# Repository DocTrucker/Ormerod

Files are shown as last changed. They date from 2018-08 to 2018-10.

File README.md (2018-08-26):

####

26/08/2018

This repository was been initially cloned from RepRapPro's repository for the 
Ormerod 2 printer. I am predominantly using this as a learning exercise but
hope in the short term to rebuild the PLA kit parts with PETG and resize a few
to reduce the stress fractures that I've experienced with a recent (old) kit 
build. My objectives are different to that of RepRapPro, therefore my ideals 
are different to their ideals. The changes I have made are not to be
interpreted as correcting mistakes, merely working to a different set of goals 
with completely different financial, engineering, and business pressures.

The work here is currently in stage one. I am currently reverse engineering 
the presented STL files into parametric FreeCAD files. My plan is as follows:

1. Re-engineer existing STL files back into a parametric FreeCAD format.
2. Build a basic assembly model to ensure the files are fit fort purpose.
3. Design parts as needed to incorporate an E3D V6 hot end and Bondtech
   Extruder.
4. Build these parts and assemble the first iteration of my take on the
   Ormerod 2.
5. Make the first release of files at this stage.
6. Carry out a written review of the parts and establish objectives to be 
   achieved before the next release.
7. Execute the changes with a modifications categorised into reliability,
   part quality, one off build cost, design for ease of build, and/or build 
   rate.
8. Following release.

I expect that I will move onto a different design of machine after stage 8.

01234567890123456789012345678901234567890123456789012345678901234567890123456789

####

The RepRapPro Ormerod 2 3D Printer design files repository

Licensed under the GPL 3, see: http://www.gnu.org/copyleft/gpl.html

For more information see: https://reprappro.com/shop/reprap-kits/ormerod-2-kit/

Files in this directory were produced in SolidWorks 2015, and is the full assembly for the Ormerod 2. Some components that are shared with our other printers may be found in our "Library" repository.

The 'STLs' directory contains STLs of the printed parts. Instructions for printing parts for Ormerod 2, and a reference - itemising part numbers, descriptions and required quantities - may be found in the Ormerod instructions, here: https://reprappro.com/documentation/ormerod-2/#Printing_parts_for_Ormerod_2

The 'dxf' folder contains the parts in a format for laser cutting.

License GPL

No guarantee is made that the files contained in this project will be free from design faults. The user accepts the risk that some issues may arise from printing and assembling the files contained within this project. Users are however encouraged to publish errors/improvements back to the originator.

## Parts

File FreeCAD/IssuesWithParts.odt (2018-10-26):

Notes on Parts

# 02_548_y-motor-bracket

Overhang to build surface on rear elongated motor bolt hole necessary?

Remove counter sinks

More bracing to hols motor secure.

Use easily accessible idler for tension rather than motor.

Groove bolt hole body could be taller to secure onto the rail better when tightened?

# 15_441_z-gear-driven

Needs to be built with brim.

# 16_492_z-bearing-clamp

(revised) Bolt boss 45 degree slope results in two sharp points trying to meet. Both curl away form intended position.

(revised) Use more of a slope from main body to boss to reduce overhangs.

(revised) Bearing centre to close to base of part.

# 18_440_z-gear

Needs to be built with brim.

# 20_446_extruder-small-gear

Needs to be built with brim.

# 21_xxx_retaining-tongue

No issues. Keying design to prevent incorrect orientation in assembly would help.

# 22_447_extruder-large-gear

Needs to be built with brim.

# 08_549_y-bearing-belt-clamp

Potentially need to lift bearing 0.1mm.

Belt too tight a fit in gripper.

# 09_550_y-bearing-clamp-tagged

Potentially need to lift bearing 0.1mm.

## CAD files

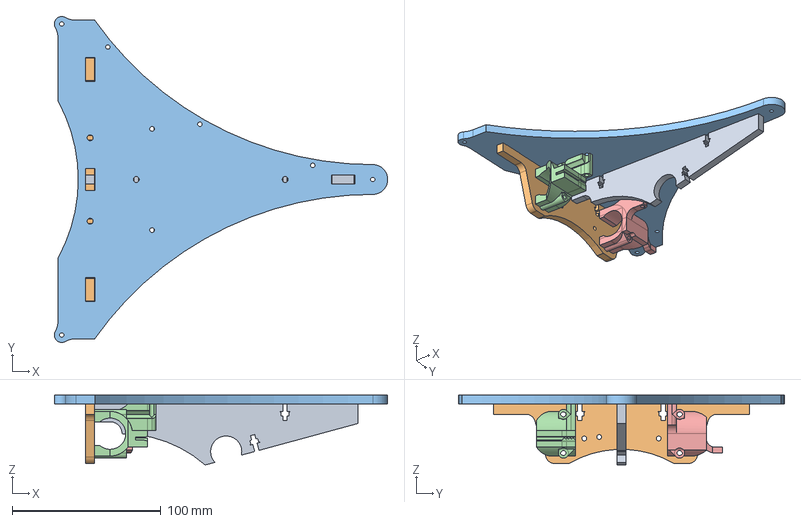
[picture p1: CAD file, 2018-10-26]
FreeCAD/build_surface_assembly.fcstd
224.0 x 219.0 x 47.0 mm

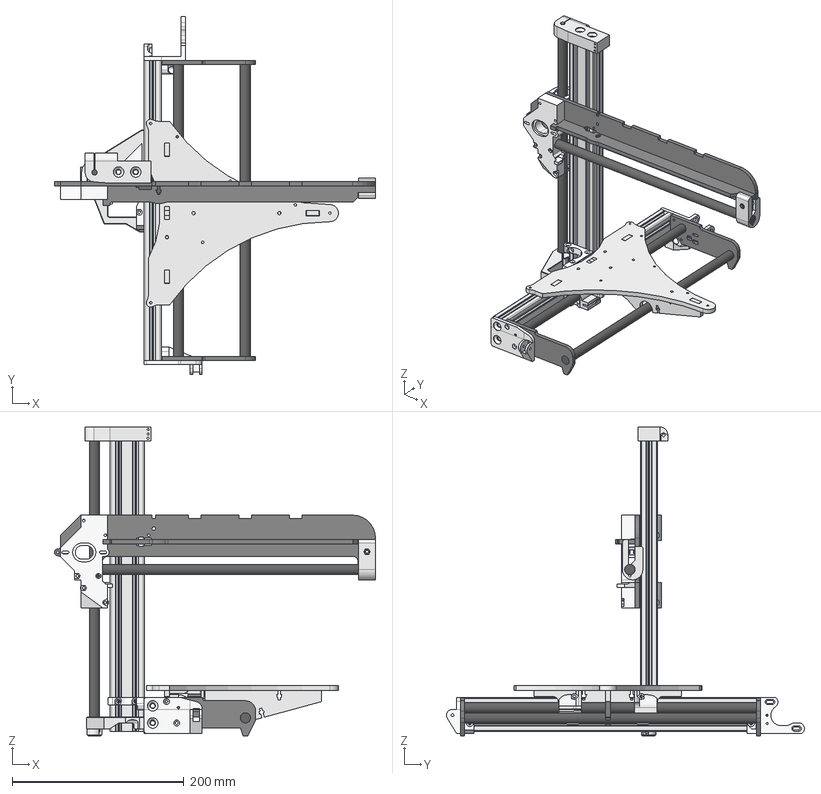
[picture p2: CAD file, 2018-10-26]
FreeCAD/all-in-assembly.fcstd
374.3 x 417.3 x 360.1 mm
y-axis-idler
SmoothRod
SmoothRod001
y-motor-bracket
z-motor-brace
SmoothRod002
SubtractiveLoft002
x-axis-plate
z-bearing-clamp
z-bearing-clamp001
x-rib
x-axis-rod
y-axis-end-plate001
y-axis-end-plate002
x-motor-bracket
z-upper-mount
z-axis-extrusion
y-axis-extrusion
z-lower-mount
x-axis-idler

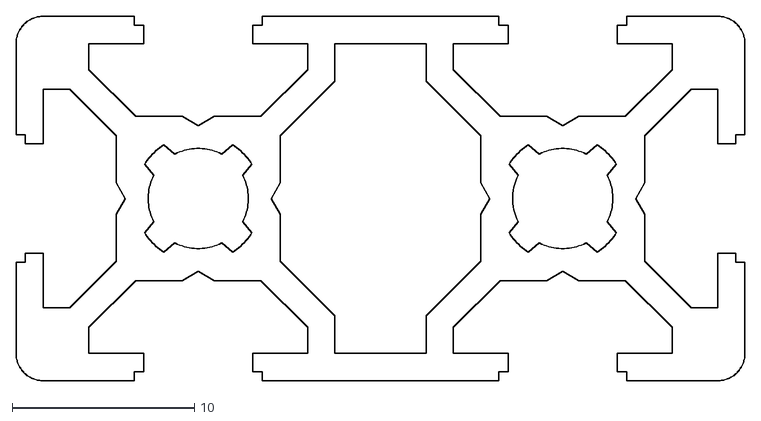
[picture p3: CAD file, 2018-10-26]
dxf/Extrusion_Profile.dxf
40.0 x 20.0

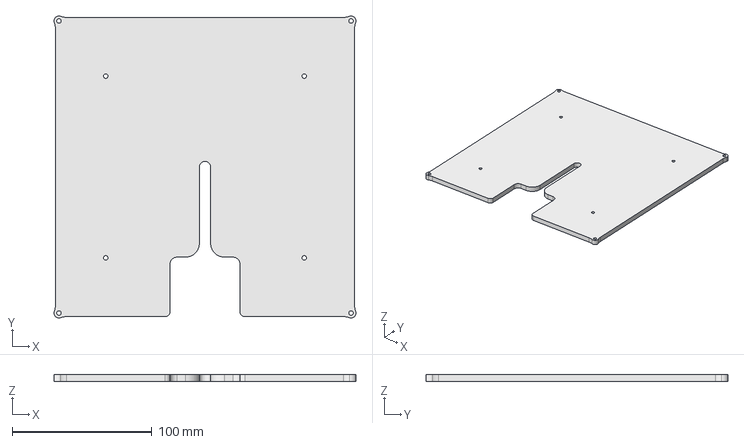
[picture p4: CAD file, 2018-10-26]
FreeCAD/xx_1044_build-surface-base.fcstd
216.1 x 216.1 x 5.00 mm

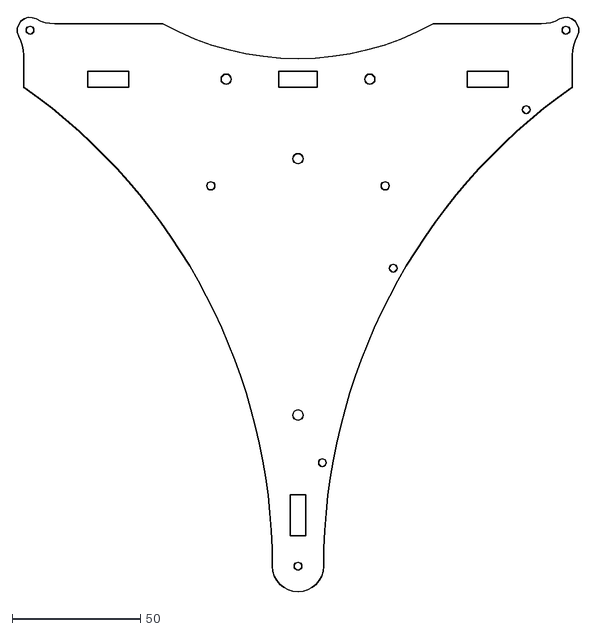
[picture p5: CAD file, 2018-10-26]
dxf/bed.DXF
219.9 x 224.5

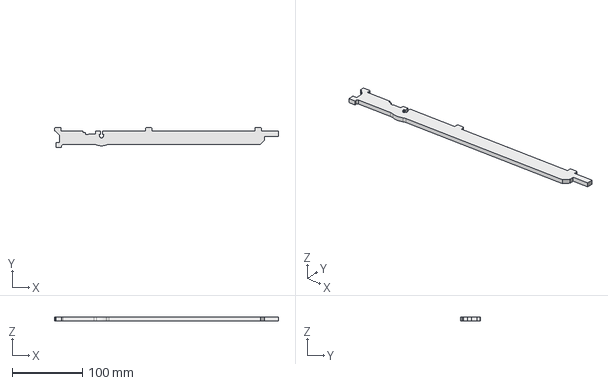
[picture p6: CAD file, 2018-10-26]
FreeCAD/xx_562_x-rib.fcstd
319.5 x 28.0 x 5.00 mm

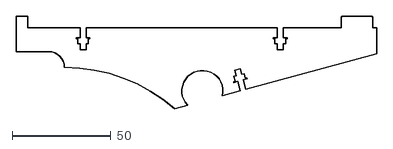
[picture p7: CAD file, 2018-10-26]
dxf/y-cross-rib.DXF
183.0 x 47.0

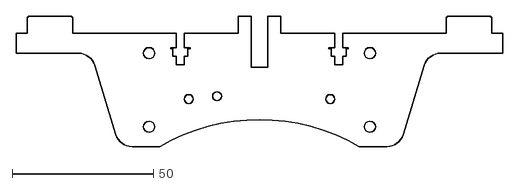
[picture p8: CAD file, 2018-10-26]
dxf/y-rib.DXF
172.0 x 46.0

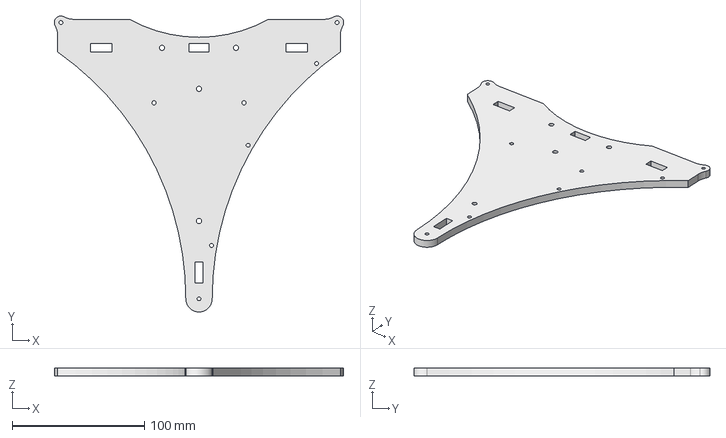
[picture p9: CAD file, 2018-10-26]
FreeCAD/xx_xxx_bed.fcstd
219.0 x 224.0 x 6.00 mm

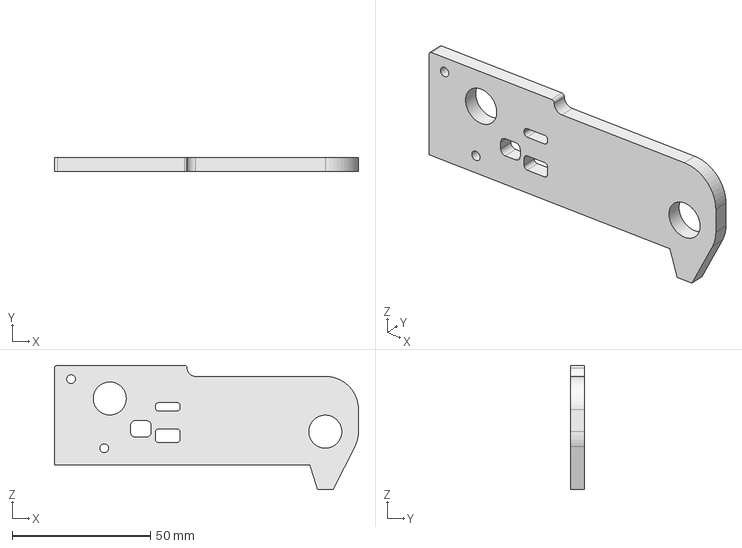
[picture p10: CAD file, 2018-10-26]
FreeCAD/xx_531_y-axis-end-plate.fcstd
110.0 x 5.00 x 45.0 mm

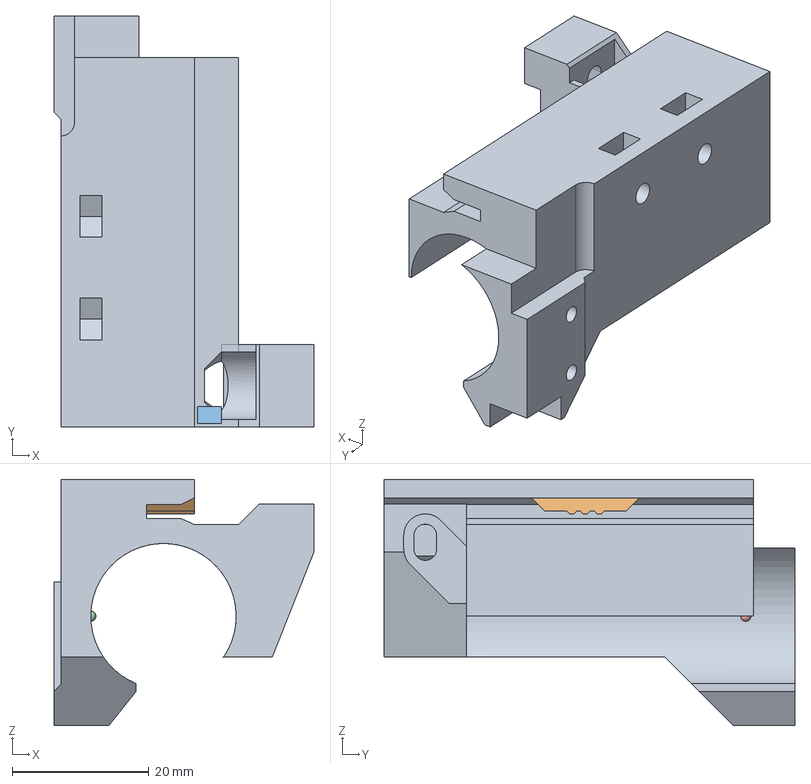
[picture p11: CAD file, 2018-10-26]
FreeCAD/11_546_x-carriage.FCStd
38.0 x 60.0 x 36.0 mm
Main Body
Belt Gripper
XRib Bearing Nut Stop
Lock Sphere 1
Lock Sphere 2

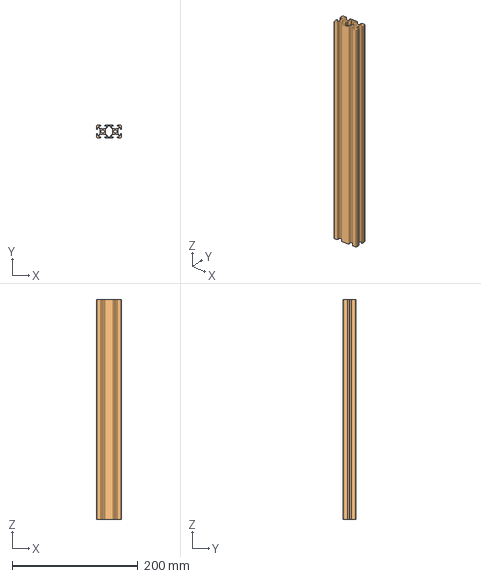
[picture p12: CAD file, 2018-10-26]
FreeCAD/xx_458_aluminimum-extrusion.fcstd
40.0 x 20.0 x 350.0 mm

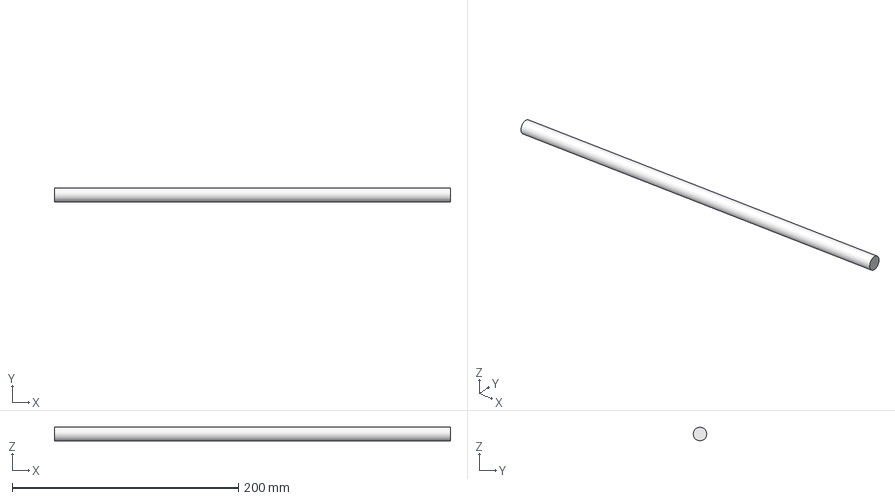
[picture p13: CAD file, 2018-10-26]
FreeCAD/xx_402_smooth-rod.fcstd
350.0 x 12.0 x 12.0 mm

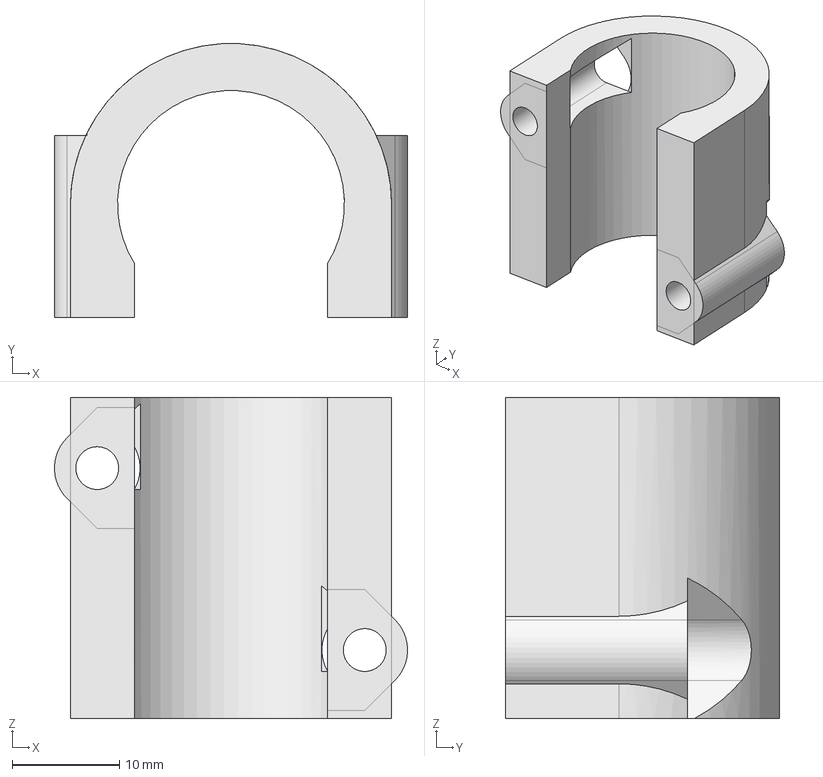
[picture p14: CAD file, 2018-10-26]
FreeCAD/16_492_z-bearing-clamp.FCStd
33.0 x 25.6 x 30.0 mm

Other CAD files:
FreeCAD/14_407_z-runner-mount.FCStd
FreeCAD/10_462_x-idler-bracket.FCStd
FreeCAD/xx_561_x-axis-plate.fcstd
FreeCAD/xx_xxx_y-cross-rib.fcstd
FreeCAD/01_547_y-idler-bracket.FCStd
FreeCAD/02_548_y-motor-bracket.FCStd
FreeCAD/03_469_z-motor-brace.FCStd
FreeCAD/04_437_z-lower-mount.FCStd
FreeCAD/05_438_z-upper-mount.FCStd
FreeCAD/06_527_z-corner-bracket.FCStd
FreeCAD/07_503_z-foot.FCStd
FreeCAD/08_549_y-bearing-belt-clamp.FCStd
FreeCAD/09_550_y-bearing-clamp-tagged.FCStd
FreeCAD/12_473_x-motor-bracket.FCStd
FreeCAD/extruder-drive-cover.fcstd
FreeCAD/xx_xxx_y-rib.fcstd

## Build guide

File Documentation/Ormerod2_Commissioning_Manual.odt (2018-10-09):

Ormerod 2 Build Manual

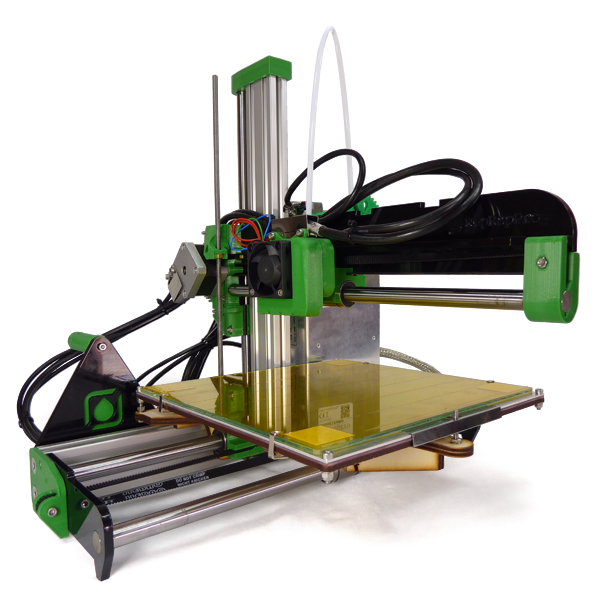
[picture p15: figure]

# Forward

## Credits & License

Original Machine Design: | Jean-Marc Giacalone Adrian Bowyer
Original Documentation: | Ian Stratford
Documentation Conversion to ODT/PDF: | Wesley Brooks
License: | GPL

## Original Documentation Hosts:

Web Archive | https://web.archive.org/web/20160106171632/https://reprappro.com/documentation/ormerod-2/
cheeseandham (RepRap Forum) | http://reprappro.cheeseandham.me.uk/reprappro.com/documentation/index.html

## This Documentation Iteration Host:

DocTrucker GitHub | https://github.com/DocTrucker/Ormerod/tree/master/Documentation

# Ormerod 2

## Overview

The RepRap Pro Ormerod 2 is the latest RepRap self-replicating 3D printer from RepRap Pro. The machine is a faster to assemble, networked 3D printer with non-contact bed probe for full geometric compensation.

These pages are the complete instructions for commissioning and using the RepRapPro Ltd (https://web.archive.org/web/20170716103559/https://reprappro.com/) version of RepRap Ormerod 2. Like all RepRap machines, RepRapPro Ormerod 2 is fully open-source. It is licensed under the GPL. All the design files and software are available from the RepRapPro Ltd Github (https://web.archive.org/web/20170716103559/https://github.com/reprappro/Ormerod) repository.

The RepRapPro Ormerod 2 is fitted with the open-source Duet electronics (https://web.archive.org/web/20170716103559/https://github.com/T3P3/Duet).

## General Notes

## Ormerod 2 Versions

Some sections of the instructions are arranged in tabs, with alternate parts and instructions, depending on the version of your kit. Below is the changelog, which shows the differences between kit versions. The tabs refer to the version number of the Ormerod kit. Your Ormerod kit version number is marked on the sticker on the power supply (on 528.2 and later kits ), or on the x-rib (for earlier kits). Use the LATEST version number – some kits have the 528.2 PSU, but the 528.1 x-rib. Use the set of instructions that relate to your printer.

528.0 | Sept 2014: Original shipping version of Ormerod 2.
528.1 | Oct 2014: Changes to packing. Acrylic fan spacer replaces printed fan-duct and nozzle-duct.
528.2 | Dec 2014: Change to supplied power supply, and added lasercut acrylic parts to mount Duet on new PSU.
528.3 | Feb 2015: Changes to packing.
528.4 | New heated bed design, new bed wiring loom.
528.5 | Ships with new Quick-set nozzle. Separate hot end and fan looms. Cooling fan and duct supplied. Small updates to some printed parts (x-carriage, z-upper-mount, y-motor-mount). Changes to packing.

## Get Support

## Tool List

### Required

Allen keys: 1.5mm, 2mm, 2.5mm, 4mm (the long reach type, with a ‘ball’ hex on the end, are very useful)

### Nice to Have, But Not Necessary

# Commissioning

https://web.archive.org/web/20160106172926/https://reprappro.com/documentation/commissioning-introduction/commissioning-duet/

# Calibration

https://web.archive.org/web/20160106173018/https://reprappro.com/documentation/commissioning-introduction/calibration-duet/

# Printing

https://web.archive.org/web/20160106191341/https://reprappro.com/documentation/commissioning-introduction/printing-duet/

# Maintenance

https://web.archive.org/web/20160106191347/https://reprappro.com/documentation/commissioning-introduction/maintenance-duet/

# Troubleshooting

https://web.archive.org/web/20160106191355/https://reprappro.com/documentation/troubleshooting-introduction/

# Wiring

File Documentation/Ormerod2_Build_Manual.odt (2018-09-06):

Ormerod 2 Build Manual

# Forward

## Credits & License

Original Machine Design: | Jean-Marc Giacalone Adrian Bowyer
Original Documentation: | Ian Stratford
Documentation Conversion to ODT/PDF: | Wesley Brooks
License: | GPL

## Original Documentation Hosts:

Web Archive | https://web.archive.org/web/20160106171632/https://reprappro.com/documentation/ormerod-2/hot-end-assembly-quick-set/
cheeseandham (RepRap Forum) | http://reprappro.cheeseandham.me.uk/reprappro.com/documentation/index.html

## This Documentation Iteration Host:

DocTrucker GitHub | https://github.com/DocTrucker/Ormerod/tree/master/Documentation

# Ormerod 2

## Overview

The RepRap Pro Ormerod 2 is the latest RepRap self-replicating 3D printer from RepRap Pro. The machine is a faster to assemble, networked 3D printer with non-contact bed probe for full geometric compensation.

These pages are the complete instructions for building, commissioning and using the RepRapPro Ltd (https://web.archive.org/web/20170716103559/https://reprappro.com/) version of RepRap Ormerod 2. Like all RepRap machines, RepRapPro Ormerod 2 is fully open-source. It is licensed under the GPL. All the design files and software are available from the RepRapPro Ltd Github (https://web.archive.org/web/20170716103559/https://github.com/reprappro/Ormerod) repository.

The RepRapPro Ormerod 2 is fitted with the open-source Duet electronics (https://web.archive.org/web/20170716103559/https://github.com/T3P3/Duet).

If you want to print the plastic parts for a RepRapPro Ormerod 2, see this web page (https://web.archive.org/web/20170716103559/https://reprappro.com/documentation/ormerod-2/printing/).

## General Notes

BEFORE YOU ATTEMPT TO ASSEMBLE ANY PART OF THE RepRapPro ORMEROD 2 3D PRINTER, PLEASE READ THESE BUILD INSTRUCTIONS FULLY AND ENSURE YOU UNDERSTAND THEM. Although all parts are covered by warranty, this will be invalidated by your not following these build instructions. You are building a complicated machine; many different skills are required to build, to commission and to operate a 3D printer. Try not to rush your build, or you may miss out something vital!

- Give yourself plenty of space and ensure your work area is clean. Dust and dirt are a 3D printer’s worst enemy.
- All printed parts have been printed on RepRapPro’s own machines. Despite the fact that these machines are highly tuned RepRap 3D printers, some holes and features may need a little fettling to get the best performance from the RepRapPro Ormerod 2. There is a video how-to on fettling 3D printed parts here on Vimeo (https://web.archive.org/web/20170716103559/http://vimeo.com/14492980).
- Before you start the build, please ensure you have all the components as listed on the packing list included in the kit. If anything is missing or damaged, please contact us through our contact page (https://web.archive.org/web/20170716103559/https://reprappro.com/support-page/).
- We understand that people may want to change aspects of the machine’s design, and in fact we encourage this as it is one of the benefits of open-source development. Before changing anything, please be aware that the RepRapPro Ormerod 2 has been designed to maximise its build volume relative to the the machine’s footprint, and as such many of its components fit closely to others. So consider your changes carefully before you try to implement them. And when you find improvements, please tell us and the world so that we can include them in future kits, and so that existing owners can upgrade their own machines.
- The RepRapPro Ormerod 2 is a robust RepRap machine once assembled; however it does require a certain amount of care during assembly. If in doubt, force is usually not the answer! There are many ways to get support and advice; see below.

## Ormerod 2 Versions

Some sections of the instructions are arranged in tabs, with alternate parts and instructions, depending on the version of your kit. Below is the changelog, which shows the differences between kit versions. The tabs refer to the version number of the Ormerod kit. Your Ormerod kit version number is marked on the sticker on the power supply (on 528.2 and later kits ), or on the x-rib (for earlier kits). Use the LATEST version number – some kits have the 528.2 PSU, but the 528.1 x-rib. Use the set of instructions that relate to your printer.

528.0 | Sept 2014: Original shipping version of Ormerod 2.
528.1 | Oct 2014: Changes to packing. Acrylic fan spacer replaces printed fan-duct and nozzle-duct.
528.2 | Dec 2014: Change to supplied power supply, and added lasercut acrylic parts to mount Duet on new PSU.
528.3 | Feb 2015: Changes to packing.
528.4 | New heated bed design, new bed wiring loom.
528.5 | Ships with new Quick-set nozzle. Separate hot end and fan looms. Cooling fan and duct supplied. Small updates to some printed parts (x-carriage, z-upper-mount, y-motor-mount). Changes to packing.

## Printing Parts for Ormerod 2

If you have bought the hardware-only version of the Ormerod 2 kit, you will want to print the parts. You may also want to print spare parts for your printer. The list below shows the part number, part name, quantity and location of the parts. Parts are available as STL and SolidWorks files, and there should also be a STEP assembly of the whole printer.

For Ormerod 2, part number 528.0 to 528.4, the easiest place to get the parts is here: https://github.com/reprappro/Ormerod/releases (https://web.archive.org/web/20170716103559/https://github.com/reprappro/Ormerod/releases)

For 528.5 onwards, we use the part number, rather than the name of the part, for the file name. For the latest version of the parts, which should be backwards compatible with all the previous versions, see the Ormerod github repository (https://web.archive.org/web/20170716103559/https://github.com/reprappro/Ormerod). Some parts common to all our machines are in the Library github repository (https://web.archive.org/web/20170716103559/https://github.com/reprappro/Library).

You can download the whole github repository, or download the parts individually; the ‘Location’ in the link below links to the stl page. This will also help you identify the parts. If you download the parts individually, make sure you download the ‘RAW’ version of the file; if you right-click on a link and download, you will end up with a file with the right name (with .stl on the end), but it will actually be an html document!

# | Description | Qty | Location

547 | y-idler-bracket | 1 | Ormerod/STLs (https://web.archive.org/web/20170716103559/https://github.com/reprappro/Ormerod/blob/master/STLs/547.STL)
548 | y-motor-bracket | 1 | Ormerod/STLs (https://web.archive.org/web/20170716103559/https://github.com/reprappro/Ormerod/blob/master/STLs/548.STL)
469 | z-motor-brace | 1 | Ormerod/STLs (https://web.archive.org/web/20170716103559/https://github.com/reprappro/Ormerod/blob/master/STLs/469.STL)
437 | z-lower-mount | 1 | Ormerod/STLs (https://web.archive.org/web/20170716103559/https://github.com/reprappro/Ormerod/blob/master/STLs/437.STL)
438 | z-upper-mount | 1 | Ormerod/STLs (https://web.archive.org/web/20170716103559/https://github.com/reprappro/Ormerod/blob/master/STLs/438.STL)
527 | z-corner-bracket | 1 | Ormerod/STLs (https://web.archive.org/web/20170716103559/https://github.com/reprappro/Ormerod/blob/master/STLs/527.STL)
503 | z-foot | 1 | Ormerod/STLs (https://web.archive.org/web/20170716103559/https://github.com/reprappro/Ormerod/blob/master/STLs/503.STL)
549 | y-bearing-belt-clamp | 1 | Ormerod/STLs (https://web.archive.org/web/20170716103559/https://github.com/reprappro/Ormerod/blob/master/STLs/549.STL)
550 | y-bearing-clamp-tagged | 1 | Ormerod/STLs (https://web.archive.org/web/20170716103559/https://github.com/reprappro/Ormerod/blob/master/STLs/550.STL)
462 | x-idler-bracket | 1 | Ormerod/STLs (https://web.archive.org/web/20170716103559/https://github.com/reprappro/Ormerod/blob/master/STLs/462.STL)
546 | x-carriage | 1 | Ormerod/STLs (https://web.archive.org/web/20170716103559/https://github.com/reprappro/Ormerod/blob/master/STLs/546.STL)
501 | nozzle-mount (one-piece nozzle, 528.4 and before) | 1 | Ormerod/STLs (https://web.archive.org/web/20170716103559/https://github.com/reprappro/Ormerod/blob/528.4/stl/individual%20parts/nozzle-mount.stl)
1079 | nozzle-mount (Quick-set nozzle, 528.5 onwards) | 1 | Ormerod/STLs (https://web.archive.org/web/20170716103559/https://github.com/reprappro/Ormerod/blob/master/STLs/1079.STL)
473 | x-motor-bracket | 1 | Ormerod/STLs (https://web.archive.org/web/20170716103559/https://github.com/reprappro/Ormerod/blob/master/STLs/473.STL)
407 | z-runner-mount | 1 | Ormerod/STLs (https://web.archive.org/web/20170716103559/https://github.com/reprappro/Ormerod/blob/master/STLs/407.STL)
441 | z-gear-driven | 1 | Ormerod/STLs (https://web.archive.org/web/20170716103559/https://github.com/reprappro/Ormerod/blob/master/STLs/441.STL)
440 | z-gear | 1 | Ormerod/STLs (https://web.archive.org/web/20170716103559/https://github.com/reprappro/Ormerod/blob/master/STLs/440.STL)
492 | z-bearing-clamp | 2 | Ormerod/STLs (https://web.archive.org/web/20170716103559/https://github.com/reprappro/Ormerod/blob/master/STLs/492.STL)
425 | z-nut-trap | 1 | Ormerod/STLs (https://web.archive.org/web/20170716103559/https://github.com/reprappro/Ormerod/blob/master/STLs/425.STL)
554 | Extruder drive block | 1 | Ormerod/STLs (https://web.archive.org/web/20170716103559/https://github.com/reprappro/Ormerod/blob/master/STLs/554.STL)
446 | Extruder small gear | 1 | Ormerod/STLs (https://web.archive.org/web/20170716103559/https://github.com/reprappro/Ormerod/blob/master/STLs/446.STL)
447 | Extruder large gear | 1 | Ormerod/STLs (https://web.archive.org/web/20170716103559/https://github.com/reprappro/Ormerod/blob/master/STLs/447.STL)
152 | Tongue | 1 | Library/STLs (https://web.archive.org/web/20170716103559/https://github.com/reprappro/Library/blob/master/STL/152.STL)
820 | PSU cover | 1 | Library/STLs (https://web.archive.org/web/20170716103559/https://github.com/reprappro/Library/blob/master/STL/820.STL)
821 | PSU brace | 1 | Ormerod/STLs (https://web.archive.org/web/20170716103559/https://github.com/reprappro/Ormerod/blob/master/STLs/821.STL)
442 | Spool spigot | 1 | Ormerod/STLs (https://web.archive.org/web/20170716103559/https://github.com/reprappro/Ormerod/blob/master/STLs/442.STL)
525 | Spool clip | 1 | Ormerod/STLs (https://web.archive.org/web/20170716103559/https://github.com/reprappro/Ormerod/blob/master/STLs/525.STL)
1123 | Cooling fan duct | 1 | Ormerod/STLs (https://web.archive.org/web/20170716103559/https://github.com/reprappro/Ormerod/blob/master/STLs/1123.STL)

## Get Support

If you find you need help or advice with assembling, commissioning or using your RepRapPro Ormerod 2 3d printer, you can use the following channels:

- Check the instructions again; we are regularly updating them with feedback from our growing user-base.
- Contact the support department of the company that sold you your printer.
- Check the RepRap community forum, Ormerod section (https://web.archive.org/web/20170716103559/http://forums.reprap.org/list.php?340).
- Contact us on our irc (internet relay chat) channel RepRapPro (https://web.archive.org/web/20170716103559/http://webchat.freenode.net/?channels=reprappro) on freenode irc
- Contact us via email; see our contact page (https://web.archive.org/web/20170716103559/https://reprappro.com/support-page/).

## Archived Documents for Older Versions

If you have an older RepRapPro Ormerod and want a past copy of this documentation see these links:

- RepRapPro Ormerod 1 Instructions (https://web.archive.org/web/20170716103559/https://reprappro.com/documentation/ormerod/)

## Tool List

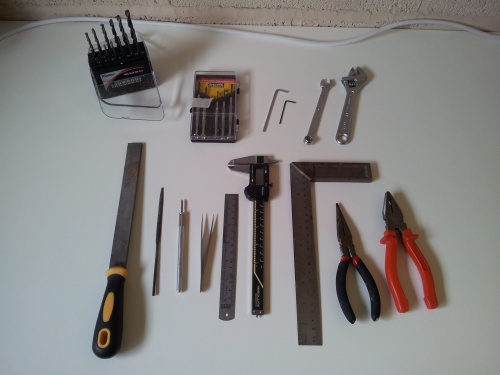
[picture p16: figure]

Tools required for the build of the RepRapPro Ormerod 2 3D printer:

### Required

Allen keys: 1.5mm, 2mm, 2.5mm, 4mm (the long reach type, with a ‘ball’ hex on the end, are very useful)

- Medium, cross-head screwdriver
- 8mm (M5) socket and/or spanner
- 15cm adjustable spanner
- Fine tweezers
- Ruler, at least 300mm
- Fine-nosed pliers
- Scissors
- Drill: 2mm
- Hand chuck, pin vice or small electric drill
- Small, flat-bladed, electrical screwdriver
- Pencil sharpener
- Digital Multimeter
- Hot air gun, or cigarette lighter (or other heat source such as a gas cooker ring for heating PTFE heatshrink; a hair dryer is not sufficient)

### For Adjusting Plastic Parts, if Necessary

- Drills: 3mm, 4mm
- File
- Half round needle file
- Sharp craft knife

### Nice to Have, But Not Necessary

# 5.5mm (M3) socket and/or spanner

- Vernier or digital callipers

# Y Axis Assembly

## Y axis sub-assemblies

### Y-idler-end

TIP: There’s a list of the Ormerod printed parts on THIS PAGE (https://web.archive.org/web/20161108033219/https://reprappro.com/documentation/ormerod-2/). Click on the ‘Location’, to see a preview of the printed part, if you’re not sure what it is.

# | Component | Qty | Type

| y-idler-bracket | 1 | Printed
| y-axis-end-plate ‘A’ | 1 | Lasercut
| M4x12mm countersunk socket head screw | 1 | Fastener
| M4 T-nut | 1 | Fastener
| M3x12mm countersunk socket head screw | 2 | Fastener
| M3 Nut | 2 | Fastener
| M3x12mm cap head screw | 1 | Fastener
| 623 bearing (10mm diameter) | 1 | Fastener

TIP: Click on pictures in the instructions to see a larger version. Right-click and select ‘Open link in new Tab’ to see the full size image.

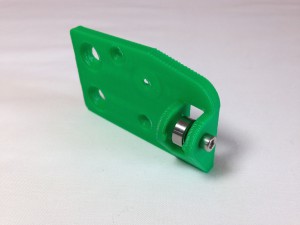
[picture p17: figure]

Fit the 623 idler bearing to the y-idler-end. It may require a fair bit of force to push the bearing into position. It is held in place by a M3x12mm cap head screw. This should self-tap into the printed part, with no need for a nut on the free end.

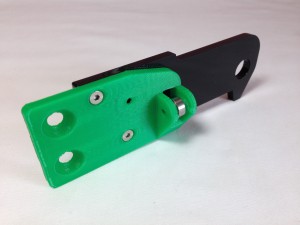
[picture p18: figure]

Using the M3x12mm countersunk socket head screws, assemble the y-axis-end-plate ‘A’ with the y-motor-bracket, with an M3 nut on the back of each screw.

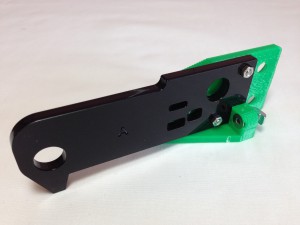
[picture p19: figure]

The M4x12mm countersunk socket-head screw goes through the y-idler-mount as shown, with the T-nut on the other side. Leave the T-nut loose – it connects with the aluminium extrusion.

### Y-motor-end

# | Component | Qty | Type

| y-motor-bracket | 1 | Printed
| y-axis-end-plate ‘B’ | 1 | Lasercut
| M4x12mm countersunk socket head screw | 1 | Fastener
| M4 T-nut | 1 | Fastener
| M3x12mm countersunk socket head screw | 2 | Fastener
| M3 Nut | 2 | Fastener

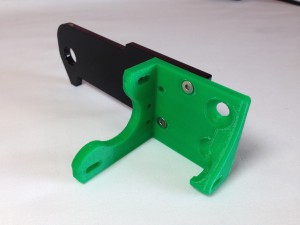
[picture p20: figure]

Begin by assembling the Y-motor-end. Use y-axis-end-plate ‘B’ (there is a small ‘B’ engraved on one side of the plate) with the y-motor-bracket. As the y-axis-end-plate is laser-cut acrylic, the 12mm holes will be slightly larger in diameter on one side of the y-axis-end-plate (the side with the letter ‘B’) which will make it easier to insert the 12mm ground steel bar later.

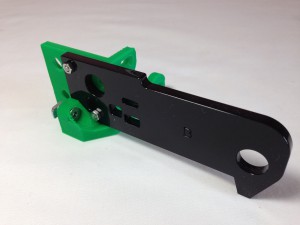
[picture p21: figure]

Using the M3x12mm countersunk socket-head screws, connect the two parts together as shown, with an M3 nut on the back of each..

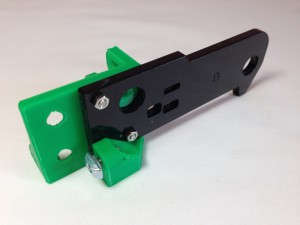
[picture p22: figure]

The M4x12mm countersunk socket-head screw goes through the y-motor-mount as shown, with the T-nut on the other side. Leave the T-nut loose – it connects with the aluminium extrusion.

## Y axis frame

The next step is to assemble the Y axis frame. For this you will need the following:

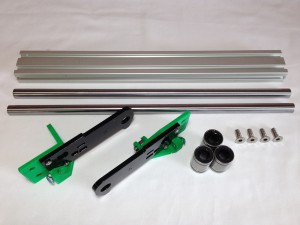
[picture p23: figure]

# | Component | Qty | Type

| y-motor-end | 1 | Assembled
| y-idler-end | 1 | Assembled
| Aluminium extrusion | 1 | Hardware
| Smooth rod 12x350mm | 2 | Hardware
| LM12UU Linear bearing | 3 | Hardware
| M6x16mm countersunk socket head screw | 4 | Fastener

Screw the y-idler-end onto the aluminium extrusion, using two M6x16mm countersunk socket screws. These screws need to be tight – if they are loose, the Y-ends will move in relation to the aluminium extrusion, and the X axis will not be level to the bed.
On the inside of the y-idler-end, check that the M4 T-nut is located in the extrusion slot.
As you tighten the screw, the T-nut should rotate 90 degrees in the extrusion, from horizontal to vertical. It may need a little help! If it can’t rotate, it may have started too close to the printed part; loosen the screw off a couple of turns, then try tightening again. Once it has rotated so that it is vertical, fully tighten the screw.
With the y-idler-end supported by the edge of a table, take one of the 12x350mm smooth rods and push it into the hole in the acrylic end piece that is closest to the aluminium extrusion. The 12mm diameter holes are sized to be an interference fit with the rods, and the Acrylic laser cut plates are quite brittle so care must be taken when inserting the rods not to break the end plates. You can use a piece of wood, or soft-faced hammer, to tap gently on the end of the rod, if necessary.
NOTE: Some 12x350mm smooth rods may be a little longer, due to variability in manufacture. The y-idler-end printed part can accommodate this, with a pocket. The other places that the rods are used can similarly accommodate these rods (Z axis), or it doesn’t matter (X axis, Y axis front rod) – the longer rod will simply poke out the end a millimetre or so.
With the acrylic supported, push the second 12x350mm smooth rod into the hole in the end of the plate. Keep the rod perpendicular to the plate whilst pushing. Try to keep both rods upright, so they do not stress the holes in the Acrylic.
Slide the LM12UU Linear bearings onto the smooth rod. Put two onto the rod closest to the aluminium extrusion, and one on the front rod. Check they slide smoothly and freely.
Push the y-motor-end onto the smooth rods at the other end. This may be easiest with the Y axis vertical. Make sure the acrylic part is supported when pushing the rods in. Try and keep the smooth rods as straight as possible, to avoid damaging the acrylic parts. Push them home, so that the motor mount is flush with the aluminium extrusion. Again, only tap them in with a piece of wood, or soft-face hammer, to avoid damaging the parts.
Screw the y-motor-end onto the aluminium extrusion, using two M6x16mm countersunk socket screws. These screws need to be tight – if they are loose, the X axis will not be level to the bed.
Ensure the M4 T-nut is located in the extrusion slot, and tighten.
The completed assembly. Check all screws are tight.

## Y Axis Motor

Now you can fit the Y axis motor. For this step you will need the following:

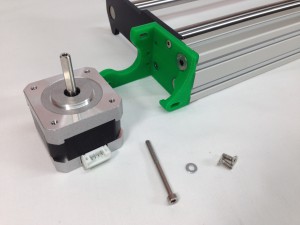
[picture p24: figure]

# | Component | Qty | Type

| y-axis-frame | 1 | Assembled
| NEMA17 stepper motor | 1 | Hardware
| M3x8mm countersunk socket screw | 2 | Fasteners
| M3x40mm cap head screw | 1 | Fasteners
| M3 washer | 1 | Fasteners

One screw needs to be removed from the back of the motor, as shown. Don’t lose this M3x26mm crosshead screw; we’ll be using it for the y-carriage.
Fit the motor into the printed y-motor-bracket. Secure the motor in place with 2 x M3x8mm countersunk socket screws in the front face.
Put one M3x40mm cap head screw with an M3 washer, in the back of the motor, where you took out the motor screw.
The three screws of the motor are mounted in slots, so you can slide the motor a small distance. This allows you to adjust the belt tension, once the belt is fitted. Leave the screws hand tight with the motor at the right-hand end of the slots in the picture.
The completed y axis assembly.

# Z Axis Assembly

As with the Y axis, the Z axis is assembled in stages, starting with small sub-assemblies which are brought together towards the end.

## Z Axis Sub-Assemblies

### Z-motor-mount

Begin with the z-motor-mount. You will need the following parts:

# | Component | Qty | Type

| z-motor-brace | 1 | Printed
| NEMA17 stepper motor | 1 | Hardware
| M3x8mm countersunk socket screw | 1 | Fastener
| M3 washer | 1 | Fastener
| 623 bearing (10mm diameter) | 1 | Hardware
| M3x12mm countersunk socket screw | 3 | Fastener
| M4x12mm countersunk socket screw | 3 | Fastener
| M4 T-nut | 3 | Fastener

Begin by securing the 623 bearing on the corner of the Z motor, with an M3x8mm countersunk socket screw. The connector at the bottom of the motor shows which corner to use. The M3 washer goes between the bearing and the motor body; check the bearing can rotate freely.
Loosely fit the M4 T-nuts with the M4x12mm countersunk screws to the z-motor-brace. Then screw the stepper motor to the z-motor-brace using the M3x12mm countersunk screws, as shown.

### Z-lower-mount

The z-lower-mount sub-assembly requires the following:

# | Component | Qty | Type

| z-lower-mount | 1 | Printed
| M4x12mm countersunk socket screw | 3 | Fastener
| M4 T-nut | 3 | Fastener

Loosely fit the M4 T-nuts as shown

### Z-upper-mount

The z-upper-mount sub-assembly requires the following:

# | Component | Qty | Type

| z-upper-mount | 1 | Printed
| M3x35mm cap head screw | 1 | Fastener
| M3 nut | 1 | Fastener

Fit the M3 screw and nut as shown.

### Z-corner-bracket (528.5 onwards)

The z-corner-bracket sub-assembly requires the following:

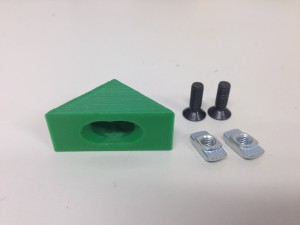
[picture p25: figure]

# | Component | Qty | Type

| z-corner-bracket | 1 | Printed
| M4x10mm countersunk socket screw | 2 | Fastener
| M4 T-nut | 2 | Fastener

Now loosely fit two M4 T-nuts using M4x10mm countersunk socket screws into the z-corner-bracket.

### Z-corner-bracket (528.0 to 528.4)

The z-corner-bracket sub-assembly requires the following:

# | Component | Qty | Type

| z-corner-bracket | 1 | Printed
| M4x12mm countersunk socket screw | 2 | Fastener
| M4 T-nut | 2 | Fastener

Now loosely fit two M4 T-nuts using M4x10mm countersunk socket screws into the z-corner-bracket.

## Z axis assembly

You can now bring all of the Z axis sub-assemblies together, using the following parts:

# | Component | Qty | Type

| z-motor-mount | 1 | Assembled
| z-lower-mount | 1 | Assembled
| z-upper-mount | 1 | Assembled
| z-corner-bracket | 1 | Assembled
| LM12UU linear bearing | 2 | Hardware
| Smooth rod 12x350mm | 1 | Hardware
| Aluminium extrusion | 1 | Hardware
| M6x16mm countersunk socket screw | 2 | Fastener

NOTE: THERE IS NO NEED TO SLIDE THE T-NUT IN FROM THE END OF THE ALUMINIUM EXTRUSION!
The M4 T-nuts are designed to drop into the extrusion slot. As the retaining screw is tightened, the T-nut rotates 90 degrees in the slot and locks into place.

Start by putting the z-upper-mount on the aluminium extrusion – it’s a tight fit. Try to put it on as squarely as possible, to avoid damaging the printed part. If you need to, use a wooden block or soft-faced hammer if you’re going to tap the aluminium extrusion, to avoid damage to the aluminium!
Check the aluminium extrusion is all the way in to the z-upper-mount. Secure the z-upper-mount with two M6x16mm countersunk screws.
Fit the 12x350mm smooth rod into the z-upper-mount. You may need to slacken off the clamp screw to get it in. Make sure it is pushed in as far as it will go; it should be level with the end of the aluminium extrusion. Tighten the clamp screw.
Slide the LM12UU Linear bearings onto the smooth rod. Check they slide smoothly and freely.
Slide the z-motor-mount sub-assembly onto the end of the extrusion. Keep all of the M4 T-nuts loose to allow for moving the motor around.
The z-lower-mount goes around the motor, and it’s easiest to put them on together.
Hook the z-lower-mount over the motor, and move them together up the aluminium extrusion. The smooth rod should engage in the hole of the z-lower-mount; make sure it is pushed on as far as possible.
Lightly tighten the two M4 T-nuts on the z-motor-mount that are engaged in the aluminium profile slot. The M4 T-nuts should not be done too tight at this stage; just enough to hold the Z motor to the extrusion.
The assembly from another angle. Try to orientate the T-nuts horizontally, so they can drop into the Y axis aluminium extrusion easily.
The complete Z axis assembly.

## Connecting the z axis assembly to the y axis assembly

On the Y axis idler side, measure 210mm from the end of the Y axis aluminium extrusion without the Y axis motor, and mark with a pencil. This is to mark where the Z axis will be connected.
On the Y axis motor side, measure 120mm from the end of the Y axis aluminium extrusion, and mark with a pencil. The Z extrusion will sit between these two marks.
The Z axis assembly can now be attached to the Y axis assembly. Orientate the Z nuts so they drop into the extrusion; you don’t need to slide them on from the end.
Tighten the three M4 countersunk screws on the z-lower-mount first. As you tighten them, the T-nuts should rotate 90 degrees and catch in the extrusion slot. They may need a wiggle to get them to turn. Do the middle one shown in the picture first; it’s the most difficult, as you can’t see if it catches, but the axis will hold when it does. Assemble loosely to start with, so you can move the components to the correct places.
The base of the vertical aluminium extrusion must be flush with the bottom of the Y axis extrusion. The bottom of the motor will be a couple of millimetres below the level of the extrusions.
Try to get the extrusion between the two marks on the Y axis aluminium extrusion, so it’s in the right place.
Use the supplied set square to check the Z axis and Y axis extrusions are at right angles to each other. Tighten the z-motor-mount to the two extrusions, then attach and tighten the z-corner-bracket, which gives additional support (shown on the left side of the Z extrusion). Repeat the above alignment steps to confirm they are all correct, before fully tightening all the fasteners.

## Attaching the z-foot

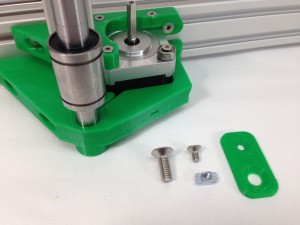
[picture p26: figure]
ORM2-z-axis-build-08

# | Component | Qty | Type | (https://web.archive.org/web/20161108034630/https://reprappro.com/wp-content/uploads/2014/05/ORM2-z-axis-build-08.jpg)

| ZY assembly | 1 | Assembled
| z-foot | 1 | Printed
| M6x16mm countersunk socket screw | 1 | Fastener
| M4x8mm countersunk socket screw | 1 | Fastener
| M4 T-nut | 1 | Fastener

The base of the vertical aluminium extrusion should be flush with the bottom of the Y axis extrusion. These two can then be secured using the z-foot, one M6x16mm countersunk socket screw, and an M4 T-nut and M4x8mm countersunk socket screw.

# Y Carriage

## Y carriage assembly

The Y carriage can now be assembled and fitted. You will need the following parts:

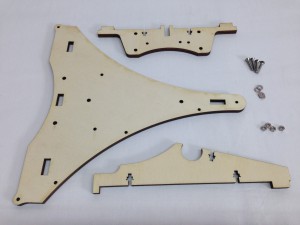
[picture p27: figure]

# | Component | Qty | Type

| bed-support (6mm ply) | 1 | Laser cut
| y-axis-rib (6mm ply) | 1 | Laser cut
| y-axis-cross-rib (6mm ply) | 1 | Laser cut
| M3x16mm countersunk socket screw | 4 | Fastener
| M3 nut | 4 | Fastener
| M3 washer | 4 | Fastener

The y-axis-rib and y-axis-cross rib slot into the bed-support. Make sure the holes in the edge of the bed-support are on the left; these are used to attach the bed wiring later.
Secure the bed-support to the Y axis ribs using the four M3x16mm countersunk socket screws. An M3 washer and M3 nut go in the captive holes of the Y axis ribs. The easiest way to do this is to hold the bed vertically, and put your finger under the hole. Drop the washer in, then the nut.
Then thread the M3x16mm countersunk socket screw through from the top of the bed-support, so it engages with the nut. Repeat for the other three nut traps between the ribs and bed-support. Tighten all of them.
Make sure the bed-insulator is orientated correctly, as shown in the picture. The holes for the wiring are on the right-hand side when the y-carriage is the correct way up as in this picture.

## Y carriage mounting

Fit the y-carriage to the assembled y-z-axis assembly. The following parts are required:

# | Component | Qty | Type

| y-z-axis assembly | 1 | Assembled
| y-carriage assembly | 1 | Assembled
| y-bearing-belt-clamp | 1 | Printed
| y-bearing-clamp-tagged | 1 | Printed
| M3x30mm cap head screw | 4 | Fastener
| M3x25mm countersunk socket screw | 1 | Fastener
| M3x26mm crosshead screw (removed from NEMA17 motor) | 1 | Fastener
| M3 nut | 6 | Fastener

Push the two bearings on the back Y rod to the extreme ends of the carriage. This gives you the space you need to mount the y-carriage.
Take an M3x30mm cap head screw, and thread it through the lower hole of the y-bearing-clamp. Note the orientation of the y-bearing-clamp in the picture. Using a pair of pliers (or fingers if they are small enough!) with an M3 nut, mount the clamp on the y-carriage, around the back smooth rod, as shown.
This can be quite fiddly! But it’s much easier without the bearings in the y-bearing-clamps. Lightly tighten the screw, as it will be easier to push the bearing in.
Lift the y-carriage up to allow you to hold an M3 nut in position, with pliers, to fix another M3x30mm cap head screw through the top hole in the y-bearing-mount.
Repeat the process for the y-bearing-mount on the other side, noting the orientation. Slide the back bearings into the y-bearing-clamps.
Note the position of the mount on the bearing. This is important to allow maximum movement of the Y axis in its frame. Slide the front bearing sideways into the notch in the Y carriage.
Using the M3x26mm crosshead screw your removed from the y-axis NEMA17 motor, push this up through the y-bearing-clamp-. If you put it in from the top, it will get in the way of the belt.
Secure with an M3 nut on top of the bed-support.
On the other side, thread a M3x25mm countersunk screw down through the bed-support, through the y-bearing-clamp, and secure with an M3 nut.
Tighten all six clamp screws. While doing this, slide the y-carriage up and down the smooth rods; this help centre the bearings, and lets the carriage slide smoothly. The picture shows the finished assembly.

## Y axis drive belt

# | Component | Qty | Type

| 1/4″ MXL Belt | 1 | Hardware
| MXL pulley | 1 | Hardware
| M3 grub screw | 1 | Hardware
| Microswitch | 1 | Electronics
| M2.5x10mm cap head screw | 2 | Electronics

The 1/4″ MXL belt is supplied as one piece. Measure it with a tape measure, and cut the MXL belt to at least 710mm for the X axis, making sure you have at least 830mm left for the Y axis. There should be more belt than you need, but DO NOT just cut it in half – it may leave with you with too little for the Y axis!
Mount the microswitch with the two M2.5x10mm cap head screws. These should self-tap into the plastic of the y-motor-mount. Do not widen these holes with a drill, or the screws won’t hold.
The switch should align with the hole in the laser cut y-axis-end-plate. Check the tab on the y-bearing-clamp hits the switch at the end of its travel.
Screw the grub screw partially into the pulley. The motor shaft has a flat on it; align the grub screw with this.
Put the pulley on the motor shaft, and tighten the grub screw using a 1.5mm Allen key.
Thread the belt through the top hole in the y-axis-end-plate, around the drive pulley, and back through the lower slot in the y-axis-end-plate. The teeth of the belt should mesh with the teeth of the pulley.
Thread the belt along the length of the Y axis. Twist the belt 180 degrees before feeding it through the through the lower slot in the idler end y-axis-end-plate, around the bearing, and back through the top slot. The twist in the belt means it will run on the bearing on the back of the belt.
The twist in the belt also means the teeth of the belt can interlock. This is used to join the belt, and fix it to the y-carriage. Pull the belt tight, interlock the teeth, then push the two belt ends into the y-bearing-clamp, as shown.
One end of the belt should finish in the clamp, while any extra belt is free to come out the end of the clamp. Adjust the belt until it is as tight as possible. It will probably still be a little loose; don’t worry, you will be able to adjust the tension.
Cut off the excess belt. Leave about 10mm projecting; you may need to remove and re-fit it one day.

## Y belt tensioning

The belt tension needs to be quite tight, or the axis will suffer from backlash, and you will not get smooth vertical walls in your prints. But the belt should not be too tight, or the motor will struggle to move the axis! To adjust the belt tension, the y-axis motor is mounted in slots. Loosen the three screws, and pull the motor away from the mount to increase the belt tension. Re-tighten the screws, keeping the motor square to the axis. It is sometimes easier to get someone to help you with this, as more than two hands are useful.
When you twang the bottom belt, which has the longest uninterrupted span, a just-audible note should be heard. For reference, the note of the lowest string of a bass guitar is suitable. This is the bottom ‘E’ string (https://web.archive.org/web/20161108040356/http://www.tunemybass.com/); search online for another audio example for reference, if you need it. Adjust the belt as required.
The completed assembly.

# X Axis Assembly

## X axis sub-assemblies

The first step is to assemble a couple of sub assemblies.

### X-axis-motor

The x-axis-motor moves the x-axis belt.

# | Component | Qty | Type

| NEMA17 motor | 1 | Hardware
| MXL pulley | 1 | Hardware
| M3 grub screw | 1 | Hardware

Screw the grub screw partially into the pulley. The motor shaft has a flat on it; align the grub screw with this. For the X axis, the pulley goes on the shaft with the pulley teeth closest to the motor body.
Put the pulley on the motor shaft, and tighten the grub screw using a 1.5mm Allen key. The pulley needs to sit right on the very end of the motor shaft, as shown in the picture.

### X-idler

The x-idler is at the other end of the x-axis from the x-motor, and carries the bearing for the x-axis belt.

# | Component | Qty | Type

| x-idler-bracket | 1 | Printed
| 623 bearing (10mm diameter) | 1 | Hardware
| M3x25mm countersunk socket screw | 1 | Fastener
| M3 Nut | 1 | Fastener

Push the countersunk screw through the x-idler-bracket. The hole may be a little tight where it breaks through to the gap in the middle of the x-idler-bracket. Place the bearing inside the x-idler-bracket and fit the M3 nut to the protruding screw.
Pull the M3 nut into the ‘nut trap’, but leave the assembly loose at this stage. A ‘nut trap’ is a hole in a printed part that is designed to hold a nut ‘captive’.

### X-carriage (528.5 Onwards)

The x-carriage is connected to the x-axis belt, and travels along the X axis, carrying the hot end.

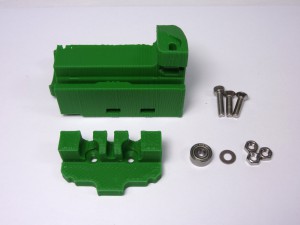
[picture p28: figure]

# | Component | Qty | Type

546.1 | x-carriage | 1 | Printed
1079 | Quick-set nozzle-mount | 1 | Printed
423 | MR93ZZ bearing (9mm diameter) | 1 | Hardware
257 | M3x12mm cap head screw | 1 | Fastener
212 | M3 washer | 1 | Fastener
258 | M3 Nut | 3 | Fastener
466 | M3x12mm countersunk socket screw | 2 | Fastener

Fit the bearing using the M3x12mm cap head screw. IMPORTANT: use a 3mm drill to clean the slot that the screw goes through; this allows you to adjust the angle of the hot end. When it is loosened off the screw needs to be able to slide in the slot.
The M3 washer should be positioned between the bearing and the x-carriage.
The M3 nut is quite fiddly to fit. It should be possible to tighten it without using a tool on it, as the flat of the nut rests against the shoulder in the printed part.
Put an M3 nut in each of the nut traps.
Attach the nozzle mount as shown with two M3x12mm countersunk socket screws.
With this version of the x-carriage, the bearing runs on the underside of the x-axis plate, rather than on the back of it. This reduces the amount of flex of the x-axis-plate.

### X-carriage (528.0 to 528.4)

The x-carriage is connected to the x-axis belt, and travels along the X axis, carrying the hot end.

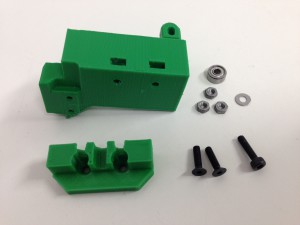
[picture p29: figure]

# | Component | Qty | Type

546 | x-carriage | 1 | Printed
501 | nozzle-mount | 1 | Printed
423 | MR93ZZ bearing (9mm diameter) | 1 | Hardware
257 | M3x12mm cap head screw | 1 | Fastener
212 | M3 washer | 1 | Fastener
258 | M3 Nut | 3 | Fastener
466 | M3x12mm countersunk socket screw | 2 | Fastener

Fit the bearing using the M3x12mm cap head screw. The M3 washer should be positioned between the bearing and the x-carriage. IMPORTANT: use a 3mm drill to clean the slot that the screw goes through; this allows you to adjust the angle of the hot end. When it is loosened off the screw needs to be able to slide in the slot.
Put an M3 nut in each of the nut traps. Attach the nozzle mount as shown with two M3x12mm countersunk socket screws.

## X axis assembly

Now you can start to assemble the X axis.

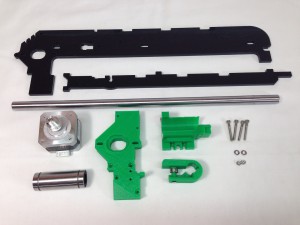
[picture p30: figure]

# | Component | Qty | Type

| x-carriage | 1 | Assembled
| x-idler | 1 | Assembled
| x-axis motor | 1 | Assembled
| x-motor-bracket | 1 | Printed
| x-axis-plate | 1 | Laser cut
| x-rib | 1 | Laser cut
| Smooth rod 12x350mm | 1 | Hardware
| LM12LUU linear bearing | 1 | Hardware
| M3x25mm cap head screw | 4 | Fasteners
| M3 Nut | 2 | Fasteners
| M3 washer | 2 | Fasteners

Push the x-rib into place in the slots in the x-axis-plate, which should slot together easily. DO NOT FORCE! Acrylic is quite brittle, and you may break the x-rib. Use a file to smooth any rough edges, and ease the tabs of the x-rib, so it goes into the x-axis-plate easily. The x-axis-plate should be perfectly flat; if it is bowed or twisted, the x-carriage will not run straight and true.
Make sure the screw through the x-idler sub-assembly is loose. Push the x-idler onto the end of the x-axis-plat and x-rib as shown, making sure it goes on straight.
Slide the smooth rod into the x-motor-bracket.
Then slide the linear bearing onto the bar, then the x-carriage. You need to fit the x-carriage now, as it won’t fit on once the smooth rod is connected to the x-idler (next step). Don’t push the x-carriage onto the bearing yet, as it needs to be off the bearing to attach the x-axis-drive-belt.
Push the smooth rod into the x-idler. Be careful not to bend or twist the acrylic parts.
Push the x-motor-bracket until it buts up to the x-rib. Ensure you have the parts lined up before applying too much pressure as the acrylic parts are not very forgiving. You may find this easier if you do it vertically, with the x motor bracket supported by the edge of a bench just under the smooth rod, but don’t let the assembly drop to the floor…
The x-carriage runner bearing should be behind the x-axis plate for the old version of the x-carriage (528.4 and earlier). If you’re using the newer version of the x-carriage (528.5 onwards), the bearing runs on the underside of the x-axis-plate. See last picture in the preceding section.
Insert two of the M3x25 screws in the top and bottom holes in the x-motor-bracket, to act as guide screws, and to hold the x-motor-bracket in place. Check that the x-motor-bracket fits in place; it may need trimming for a good fit around the x-rib. Make sure all the M3 holes in the printed part line up with the laser cut part – trim as necessary. Put an M3 nut in each nut trap, as shown.
The smooth rod should butt up to the end of the x-motor-bracket, as shown. Insert two M3x25mm cap head screws to engage with the M3 nuts in the nut traps. Tighten the screws.
Remove the two M3x25mm screws that you put in as guide screws. Insert them, with washers on, to mount the motor. Orientate the motor as shown, with the wiring connector pointing out and down from the axis. Do not fully tighten the screws; the motor is mounted in slots to allow for tensioning the x-axis-drive-belt. Slide the motor to the end of the slots nearest the x idler bracket.
Tighten the countersunk screw in the x-idler-bracket.
The completed assembly.

### Z-runner-mount

The z-runner-mount sub-assembly stops the x-axis rotating around the z-axis.

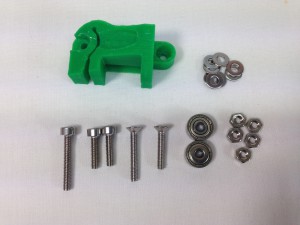
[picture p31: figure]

# | Component | Qty | Type

| z-runner-mount | 1 | Printed
| 623 bearing (10mm diameter) | 2 | Hardware
| M3x20mm cap head screw | 1 | Fastener
| M3x12mm cap head screw | 2 | Fastener
| M3x20mm countersunk socket screw | 1 | Fastener
| M3x16mm countersunk socket screw | 1 | Fastener
| M3 Nut | 5 | Fastener
| M3 washer | 9 | Fastener

Put an M3 nut in each nut trap. Make sure they are at the bottom of the nut traps. If they don’t drop straight in, pull them into the nut traps with an M3 screw. Using one M3x20mm cap head screw and one M3x12mm cap head screw, attach the bearings. Put one bearing on each screw, then 4 x M3 washers between each bearing and the z-runner-mount.
Assemble as shown in the picture.
Put the M3x20mm countersunk screw through the recessed hole in the z-runner-mount.
Put your finger under the captive hole in the x-rib, and drop an M3 washer and M3 nut into it. Mount the z-runner-mount assembly to the x-axis-plate, putting the M3x20mm countersunk screw through the x-axis-plate and into the x-rib, where it is secured by the captive M3 nut and washer.
Use the M3x12mm cap head screw, which goes through the x-axis-plate and into the top hole of the z-runner-mount, and is secured with an M3 nut. Check both bearings are free to rotate; add or remove a washer if the bearing in the x-axis-plate is touching the acrylic.
Use an M3x16mm countersunk socket screw and M3 nut to secure it. DO NOT OVER-TIGHTEN! The z-runner-mount should only need to lightly hold the z axis aluminium extrusion, or the axis will be difficult to move.

### X axis drive belt

To finish the X axis, attach the drive belt.

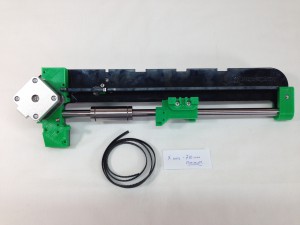
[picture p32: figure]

# | Component | Qty | Type

| x-axis assembly | 1 | Assembled
| MXL belt | 710mm | Hardware

The X axis drive belt can now be fitted. The 1/4″ MXL belt should be accurately cut to 710mm in length. Insert the belt through the slot in the x-motor-bracket, around the drive pulley and back out through the second slot.
This is quite fiddly; moving the motor back and forth will help feed the belt through, as will rotating the motor pulley. You can also push the belt around the back of the pulley, with a small Allen key or screwdriver.
Twist the top section of belt 180 degrees, and pass it over and around the idler bearing. The smooth side of the belt will be in contact with the bearing.
Slide the end of the lower section of belt, from the motor end, into the x-carriage. The end of the belt should be flush with the end of the x-carriage if your belt has been cut to 710mm. Mesh the teeth of the two ends of the belt, and push it into the slot in the x-carriage.
Make sure the belt is pushed fully back in the slot, and that there is as much engagement of the teeth as shown.
The linear bearing can now be slid into the x-carriage.
Tighten the belt by sliding the X axis motor back. Tighten the motor mounting screws.

The completed assembly. Check the x-carriage runs smoothly by moving the x-carriage up and down the smooth rod. If it sticks, the bearing may need lubricating. It’s actually the rubber seals on the bearing ends that need lubrication; use a drop of light oil (like 3-in-1 oil or similar) on each side of the bearing and run it up and down. A remaining film of oil on the rod is good. But make sure there are no drips. Also check the belt doesn’t rub at either end; this is usually signified by a little black ‘dust’, which is where the edge of the belt is rubbing. Check the alignment of the motor pulley. If you do the x-idler up very tight, you may need to put an M3 washer on one side of the bearing, to give the belt a little more space.

# X Axis Mounting

The X axis assembly can now be mounted to the previously assembled ZY assembly.

## Z axis leadscrew

The Z axis leadscrew moves the X axis up and down.

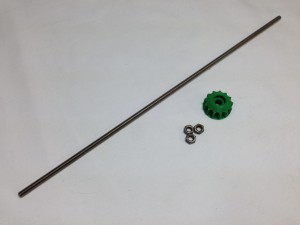
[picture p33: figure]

# | Component | Qty | Type

| z-gear-driven | 1 | Printed
| M5 threaded z-rod | 1 | Hardware
| BZP M5 nut | 3 | Fastener

Make sure the M5 threaded z-rod is clean, with no swarf or other debris in its threads. Screw two M5 nuts onto one end of the M5 threaded z-rod. Tighten one nut against the other, so that they are locked in place, right at the end of the rod.
Push the z-gear-driven onto the locked M5 nuts. The bottom nut of the two should fit into the nut trap in the gear.
Screw the last M5 nut onto the z-rod. It should look like this, when assembled. You can lightly oil the threaded rod; see the Maintenance section later in the instructions for guidance.

## X axis assembly

Now, the x-axis-assembly can be mounted on the z axis. For this, the following parts are required:

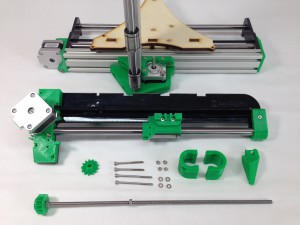
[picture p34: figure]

# | Component | Qty | Type

| x-axis-assembly | 1 | Assembled
| y carriage and z axis | 1 | Assembled
| z-axis-leadscrew | 1 | Assembled
| z-bearing-clamp | 2 | Printed
| z-nut-trap | 1 | Printed
| z-gear | 1 | Printed
| M3x50mm cap head screw | 2 | Fastener
| M3x40mm cap head screw | 2 | Fastener
| M3 Nut | 4 | Fastener
| M3 washer | 4 | Fastener

Press the z-gear onto the z-motor shaft, conical side down. The z-gear has a flat in the hole, that should align with the flat on the motor shaft, which stops the gear rotating on the shaft. The gear should be a tight fit, so make sure you line it up before pushing the gear on the motor shaft.

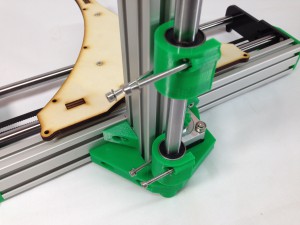
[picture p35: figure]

Slide a z-bearing-clamp onto each z axis linear bearing. Place the two M3x50mm cap head screws in the top mount, and the two M3x40mm cap head screws in the bottom mount, with a washer under each head.
Take the x-axis-assembly. Hook the z-runner-mount bearing around the z axis aluminium extrusion.
Offer up the x-axis-assembly and push the four z-bearing-mount screws through the X axis. The X axis can now sit at the bottom of the Z axis.
Use two M3 nuts to secure the bottom z-bearing-mount. Don’t do them up too tight yet.
Use a screw to pull an M3 nut into the recessed nut trap, in the z-nut-trap printed part.
You may need to push the M3 nut into the nut trap with a screwdriver, but the screw will help to align it correctly. Remove the screw once it is held in place.
Push the z-nut-trap onto the end of the 50mm cap head screws, add the remaining M3 nut, and do up the screws, but not tight.
Now tighten the bearing mount screws. The holes in the bearing clamps are clearance for the M3 screws, so keep moving the axis up and down between turns of each screw. This will let the bearings settle in the right place, and ensure that the axis runs smoothly.
Lift the X axis to the top of the Z axis, and carefully feed the z-axis-leadscrew assembly up through the z-nut-trap.
The z-axis-leadscrew sits on the 623 bearing on the corner of the Z axis motor, engaging with the z-gear on the motor.
The x-axis-assembly can now be supported by the loose M5 nut on the z-axis-leadscrew. Gently lower the X axis onto it, being careful to orientate the M5 nut correctly – see picture.
The completed assembly. Put a little light oil on the Z-axis M5 screw using a cloth. An thin even spread without drips is best.

## Checking for play in the x axis

Adjusting the z-runner-mount.

Rotation of the x-axis around the z-axis is prevented by the z-runner-mount. It is important that the z-axis aluminium extrusion is held securely by the bearings in the z-runner-mount. The outer bearing on the z-runner-mount is mounted on a hinged clamp, which allows the tension to be adjusted. However, don’t over-tighten this, or movement of the Z axis may be compromised.

# Heated Bed Assembly

## Bed thermistor assembly

The bed thermistor measures the temperature of the heated bed.

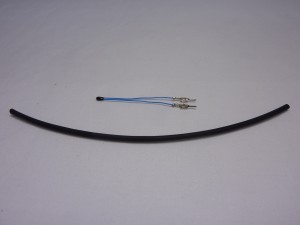
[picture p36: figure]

# | Component | Qty | Type

| 10k (bed) Thermistor | 1 | Electronics
| Black heatshrink | As required | Electronics

Cut two pieces of heatshrink, about 20mm in length.
Fold the sharp parts of the crimp, on the sides, in with a pair of pliers; this ensures that they do not cut through the heatshrink, and cause a short circuit later. Cover each crimp with a short piece of heatshrink, and use a hot air source or cigarette lighter to shrink it into place, leaving the pins exposed. If you use a flame, waft the shrink above the flame. Don’t play the flame directly on the shrink, or you will burn it. Check that the crimp, except for the pins, is insulated.

## Heated bed assembly (528.4 Onwards)

The heated bed helps the extruded plastic stick to the build surface, and improves the print quality.

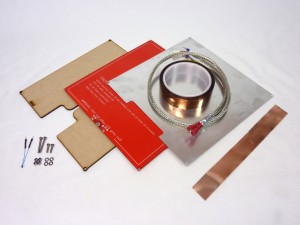
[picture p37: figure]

# | Component | Qty | Type

| Heated bed wiring loom | 1 | Heated bed
| MDF bed insulator | 1 | Heated bed
| PCB heated bed | 1 | Heated bed
| Aluminium heat spreader | 1 | Heated bed
| Kapton tape | As required | Hardware
| Metal tape | 1 | Heated bed
| Thermistor assembly | 1 | Assembled
| M3x25mm cap head screw | 2 | Fastener
| M3x12mm cap head screw | 2 | Fastener
| M3 washer | 4 | Fastener
| M3 nyloc nut | 4 | Fastener

Bend the thermistor bead at 90 degrees to the wire.
The thermistor bead fits into the central hole in the heated bed PCB. Secure it in place with some Kapton tape, with the legs of the thermistor pointing towards the PCB contacts.
Make sure the thermistor protrudes through the hole in the PCB a little. It will then have good contact with the aluminium heat spreader, and temperature readings will be more accurate.
It’s a good idea to put a piece of Kapton tape over the bed contacts, so you cannot inadvertently short circuit the bed.
Put heatshrink on the female crimps of the two smaller wires of the wiring loom, if there is none. Covering any exposed metal, but leave the hole in the end of the crimp clear. These wires connect to the thermistor and have to be insulated from each other, and any other part of the heated bed, or you will get incorrect temperature readings, or possibly short circuit the thermistor.
Connect the wiring loom to the thermistor. The thermistor has no polarity, so it doesn’t matter which way around you connect them. The thermistor wires need to sit in the slot of the MDF bed insulator. Hold It in place with a piece of Kapton tape. Put this over the connection between the thermistor and the loom; it’s extra insulation in case there is metal poking through, that could come in contact with the metal tape, which is fitted in the next step.
Tape the wires in place with the metal tape, checking the wires sit between the MDF bed insulator. This shields the thermistor wire from Electro Magnetic Interference (EMI).
Push the bed wiring loom crimps onto the tabs on the heated bed. Make sure they are pushed fully on. The bed has no polarity, so they can go on either way around. The wires will be closer to the bed if you put the flat side of the crimp towards the bed, as shown.
CAUTION! Wipe the aluminium heat spreader with a paper towel, to remove any metal swarf, and carefully check it for damage, burrs or projections before final assembly. Any scrapes or sharp protrusions from the aluminium heat spreader may scratch the PCB, and short circuit through the aluminium heat spreader, which may result in damage to the electronics.
Line up the aluminium heat spreader with the PCB, making sure that it doesn’t touch the contacts.
Turn the bed over, and put the MDF bed insulator in place.
Now assemble the heated bed by putting two M3x12mm cap head screws through the two corners of the bed at the connector end, each side of the PCB contacts. The order should be aluminium heat spreader, PCB, MDF, M3 washer, M3 nyloc nut.
Put two M3x25mm cap head screws through the back corners of the bed. The order should be: aluminium heat spreader, PCB, MDF, M3 washer, M3 nyloc nut.
Test the thermistor wiring at the end of the wiring loom; the resistance should be around 10k ohms. It was a warm day when we took this picture, around 28C, so the reading is lower, at 8.48k ohms. Remember that you have a resistance, which will become apparent with a wrong value if you hold both wires in your fingers…
Test the heated bed power wires are making a good connection by testing the resistance. This measures the resistance of the heated bed, and it should be around 1.3 ohms. You may need to wait for a few seconds for the figure to stabilise. Make sure you have a good battery in your multimeter and check that when you short its leads it reads 0 ohms, or your reading may be inaccurate.
Finally, test there is NO continuity (i.e. infinite resistance) between the aluminium heat spreader and the contacts of the heated bed. If there is continuity, there is a connection between them somewhere, and possibly the heated bed PCB has been damaged. See the earlier warning in red in this section.
The completed heated bed assembly.

## Heated bed assembly (528.0 to 528.3)

The heated bed helps the extruded plastic stick to the build surface, and improves the print quality.

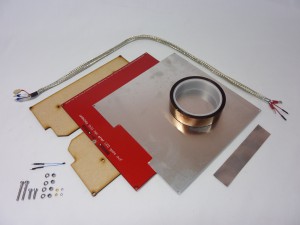
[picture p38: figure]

# | Component | Qty | Type

| Heated bed wiring loom | 1 | Heated bed
| MDF bed insulator | 1 | Heated bed
| PCB heated bed | 1 | Heated bed
| Aluminium heat spreader | 1 | Heated bed
| Kapton tape | As required | Hardware
| Aluminium tape | 1 | Heated bed
| Thermistor assembly | 1 | Assembled
| M2 spring washer | 2 | Fastener
| M2 nut | 2 | Fastener
| M3x25mm cap head screw | 2 | Fastener
| M3x12mm cap head screw | 2 | Fastener
| M3 washer | 4 | Fastener
| M3 nyloc nut | 4 | Fastener

The thermistor bead fits into the central hole in the heated bed PCB. Secure it in place with some Kapton tape, with the legs of the thermistor pointing towards the PCB contacts.
Make sure the thermistor protrudes through the hole in the PCB a little. It will then have good contact with the aluminium heat spreader, and temperature readings will be more accurate.
It’s a good idea to put a piece of Kapton tape over the bed contacts, so you cannot inadvertently short circuit the bed. (The rest of the pictures in this sequence do not show this, but fit it now.)
Put heatshrink on the female crimps of the two smaller wires of the wiring loom, if there is none. Covering any exposed metal, but leave the hole in the end of the crimp clear. These wires connect to the thermistor and have to be insulated from each other, and any other part of the heated bed, or you will get incorrect temperature readings, or possibly short circuit the thermistor.
Connect the wiring loom to the thermistor. The thermistor has no polarity, so it doesn’t matter which way around you connect them. The thermistor wires need to sit in the slot of the MDF bed insulator.
IMPORTANT: Hold the thermistor wires in place with a piece of Kapton tape. Put this over the connection between the thermistor and the loom; it’s extra insulation in case there is metal poking through, that could come in contact with the metal tape, which is fitted in the next step. | PICTURE TO COME
Tape the wires in place with the metal tape, checking the wires sit between the MDF bed insulator. This shields the thermistor wire from ElectroMagnetic Interference (EMI).
Connect the crimped eyelets to the M2 brass screws. The sequence should be eyelet – spring washer – M2 nut. Make sure the crimped eyelets are flat against the bed; they won’t fit on the brass screws if they are the other way up.
The power terminals should fit into the MDF bed insulator as shown. Get them in the correct place before fully tightening.
CAUTION! Wipe the aluminium heat spreader with a paper towel, to remove any metal swarf, and carefully check it for damage, burrs or projections before final assembly. Any scrapes or sharp protrusions from the aluminium heat spreader may scratch the PCB, and short circuit through the aluminium heat spreader, which may result in damage to the electronics.
Line up the aluminium heat spreader with the PCB, making sure that it doesn’t touch the contacts.
Now assemble the heated bed by putting two M3x12mm cap head screws through the two corners of the bed at the connector end, each side of the PCB contacts. The order should be aluminium heat spreader, PCB, MDF, M3 washer, M3 nyloc nut.
Put two M3x25mm cap head screws through the back corners of the bed. The order should be: aluminium heat spreader, PCB, MDF, M3 washer, M3 nyloc nut.
Test the thermistor wiring at the end of the wiring loom; the resistance should be around 10k ohms. It was a warm day when we took this picture, around 28C, so the reading is lower, at 8.48k ohms. Remember that you have a resistance, which will become apparent with a wrong value if you hold both wires in your fingers…
Test the heated bed power wires are making a good connection by testing the resistance. This measures the resistance of the heated bed, and it should be around 1.3 ohms. You may need to wait for a few seconds for the figure to stabilise. Make sure you have a good battery in your multimeter and check that when you short its leads it reads 0 ohms, or your reading may be inaccurate.
Finally, test there is NO continuity (i.e. infinite resistance) between the aluminium heat spreader and the contacts of the heated bed. If there is continuity, there is a connection between them somewhere, and possibly the heated bed PCB has been damaged. See the earlier warning in red in this section. You can cover any exposed copper on the heated bed with a small piece of Kapton tape, then re-assemble the bed and test again.
The completed heated bed assembly.

## Mounting the heated bed

The heated bed can now be mounted on the x-carriage.

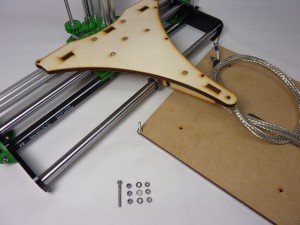
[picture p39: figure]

# | Component | Qty | Type

| Printer assembly | 1 | Assembled
| M3x25mm cap head screw | 1 | Fastener
| M3 washer | 3 | Fastener
| M3 nut | 4 | Fastener
| M3 nyloc nut | 3 | Fastener

Put the M3x25mm cap head screws up through the end of the y-carriage, as shown. Put an M3 washer on, then an M3 nut, and tighten. The M3 nyloc nut goes on part-way. The heated bed will sit on this, and it will provide adjustment for levelling the heated bed manually.
Put the other two M3 nyloc nuts on the M3x25mm cap head screws on the heated bed. These will provide levelling adjustment for the back of the bed.
Use two cable ties to loosely attach the heated bed wiring to the edge of the y-carriage. This is important; it stops the hot end cable moving at the connections. The cable will bend along it’s length as the y-carriage moves, not at one point.
Place the heated bed assembly on the y-carriage. It is mounted on three points, and the nyloc nuts provide manual height adjustment. Put the two M3 washers on top of the y-carriage, so that the two M3 nyloc nuts at the back of the bed rest on them.
Use two M3 nuts as lock nuts under the y-carriage. You can move the y-carriage to the far end to make it easier to put them on.
Slide the y-carriage to the other end of the axis to put the other M3 nut on.
The final M3 nut fits on top of the heated bed PCB, on the M3x25mm screw that points upwards through the end of the y-carriage. It holds the front of the heated bed down. The M3 nut is not shown in this picture, but put it in it’s place!

## Print surface

The glass print surface must be prepared before fitting onto the machine.

# | Component | Qty | Type

| Glass plate standard float glass, 200mm x 214mm x 3mm | 1 | Heated bed
| Plain white paper or adhesive labels | 1 | not supplied
| Kapton tape | 1 | Consumable
| Picture frame clips | 4 | Hardware

Cut the plain white paper into four 25mm x 25mm squares. Alternatively, you can use white adhesive labels, which makes it easier to stick them on the glass before covering them with Kapton. Stick the paper squares to the four corners of the glass plate, roughly 5mm from the edge. These will act as targets for the proximity sensor, for homing the Z axis, and for bed levelling. The paper targets are on top of the glass, not underneath, so we can use the close accuracy of the proximity sensor.
Cover the glass plate and paper targets with one layer of Kapton tape. We stick the Kapton tape to the top edge of the glass, then pull enough out to cover one length. Put a little tension on the tape to keep it straight, then lower it onto the glass. Work down the tape with your finger, flattening it onto the glass, and pushing out any air bubbles.
We find it easiest to work on the edge of the table, to drop the Kapton tape roll over the edge. Trim the excess off as we go. Take care to exclude bubbles; working on a white surface helps to spot them. Don’t pull the tape too taught before you lay it down. Gaps between the strips are preferable to overlaps.
Completely cover the glass, then trim any excess off flush with the edge. Try not to wrap the Kapton tape under the glass. Another way to apply the Kapton tape is to slide it on with soapy water, move it into position, then squeegee out the water. You have to wait for it to dry out before use.
The Kapton is used as the print surface, so the bed should be installed Kapton-side-up. The other side is plain glass, and sits against the aluminium heat spreader. The paper targets should be on top of the glass, and the Kapton on top of the paper targets and glass.
Install the print surface on the heated bed with the clips provided. The glass side should be in contact with the aluminium heat spreader. The clips go around the glass and the heated bed.
Locate the tab on the end of the clip in the hole in the MDF, which will hold the clip in place.

It is important that the print surface is kept free from dirt and oil, including fingerprints; these will stop your prints sticking to the bed. Wipe it clean with a paper towel and acetone (commonly found in nail polish remover, though be careful that does not contain lanolin or any other oil or grease – read the ingredients on the label). isopropyl alcohol, white methylated spirits and white vinegar should also work – all of these are organic solvents, and dissolve oil and grease into the towel before the residue evaporates. Don’t use Windex/Windowlene or polish; they often have a non-stick component!
The completed assembly.

# Extruder Drive Assembly

This section shows you how to assemble the extruder drive. All the parts for the extruder drive, except for the NEMA17 motor, should be in the bag labelled ‘Extruder drive set’.

## Extruder body

The extruder body holds the stepper motor, which drives the plastic filament.

# | Component | Qty | Type

| NEMA17 motor | 1 | Hardware
| Extruder drive block | 1 | Extruder drive
| Extruder small gear | 1 | Extruder drive
| Retaining tongue | 1 | Extruder drive
| 623 bearing (10mm diameter) | 1 | Extruder drive
| M3 washer | 1 | Extruder drive
| M3x12mm countersunk socket screw | 3 | Extruder drive

Take the extruder body, one M3x12mm countersunk screw, the 623 bearing and an M3 washer.
Put the screw in from the back, in the hole in the corner of the extruder block. Put the 623 bearing in the hole, on the screw. Put the washer on top of the bearing, as shown. This washer is sandwiched between the bearing and the motor; without it, the bearing will bind on the motor and not turn, and the extruder drive will function poorly.
Fit the motor on top of the washer and bearing. Do the screw up loosely.
Screw the other two M3x12mm countersunk screws through the extruder body and into the motor, to mount the motor solidly. Tighten all three screws. Check that the bearing can turn freely.
Push the small gear onto the motor shaft. This should be a tight fit. Ensure the flat part of the bore of the gear is aligned with the flat on the motor shaft before applying too much force. The gear has a small lip at the bottom of the teeth. This side must be against the drive block face. There should be a small gap (0.5mm to 1mm) between the gear and the face of the extruder body. If you put a piece of folded paper under the gear when you push it down this will set that gap. Pull the paper out. Check the motor turns freely.

## Large extruder gear

The large extruder gear drives the filament through the Bowden tube and into the hot end.

# | Component | Qty | Type

| Extruder large gear | 1 | Extruder drive
| Hobbed insert | 1 | Extruder drive
| M3 washer | 2 | Extruder drive
| M3 nyloc nut | 1 | Extruder drive
| M3x25mm hex head screw | 1 | Extruder drive
| MR93ZZ bearing (9mm diameter) | 2 | Extruder drive

Push the M3x25mm hex head screw through the gear. The hexagon head of the screw should be held tightly by the plastic part. Slide the two M3 washers on to the screw, followed by one MR93ZZ bearing, then the hobbed insert. The insert is symmetrical so it doesn’t matter which way round it is fitted, but it needs to be screwed tight. Most pairs of pliers have half-round holes in their jaws; use these to grip the hobbed insert. Tightening the insert pulls the hex head screw into the gear, and locks the bearing and hobbed insert in place.
Slide second MR93ZZ bearings on, followed by the M3 nyloc nut. Tighten the nut hard against the bearing. Don’t hold the hobbed insert to tighten this nut, as that will tend to loosen the insert. Hold the gear instead.
Now push the large extruder gear sub-assembly into place in the extruder body. With filament loaded, the gear can’t come out, but without filament, you should be able to pull the gear off for easy cleaning of the hobbed insert.

Make sure the gap behind the gear is correct, and turn the large gear a few times to check it is meshing smoothly with the small gear. If it isn’t, check that the large gear isn’t too close to the extruder body; it may bind with the lip on the bottom of the small gear. You may also need to file the teeth of the small or large gear, if there are any inconsistencies due to manufacture. Feed a short length (200 mm or so) of filament into the drive. When it is engaged with the hobbed insert and you hold the large gear still it should be impossible to pull the filament out of the drive using your fingers. Wind the test filament out.

## The retaining tongue

This secures the Bowden cable from the hot end into the extruder drive.

The retaining tongue that is included in the extruder drive set.
For safe keeping, insert it in the drive. It goes in with the forks of the tongue upwards.
It should hold itself in the drive.
The finished assembly.

## Mounting the extruder drive on the printer

The extruder drive assembly can now be mounted on to the machine.

The x-axis-plate has three slots that the extruder drive can fit into. The standard wiring will reach to the first or second slot. Drop the drive into the first slot, then the end of the extruder body fits into a slot in the x-rib. It is held in place by the weight of the motor.

# Hot End Assembly (Quick-set)

## Which hot end?

All Ormerod 2 528.5 and onwards kits ship with the new ‘Quick-set’ nozzle. This page has the instructions for that nozzle.

This is the Quick-set nozzle, supplied with Ormerod 2 528.5 and onward kits. If your nozzle looks like this, please use the instructions on this page.
This is the one-piece stainless steel nozzle. If you nozzle looks like this, please use the instructions on the ‘Hot end assembly (https://web.archive.org/web/20160106171632/https://reprappro.com/documentation/ormerod-2/hot-end-assembly/)‘ page.

## Building the hot end

### Assembling the hot end parts

All the parts for the hot end, like the extruder, come in one bag.

### The Bowden tube and nozzle

The Bowden tube guides the filament from the extruder to the hot end, where the filament is melted and extruded through the nozzle.

# | Component | Qty | Type

1055 | 4mm PTFE Bowden tube | 1 | Hot end
106.1 | Brass Bowden start | 1 | Hot end
738 | Quick-set nozzle (0.5mm) | 1 | Hot end
739 | Quick-set heater block | 1 | Hot end
794 | Quick-set Tapered brass M4 nut | 1 | Hot end

Start by building the hot end. Take the nozzle, aluminium heater block and tapered brass nut. Screw the heater block onto the nozzle, as tight as you can, but with fingers only. If you use pliers to hold the nozzle, and a spanner on the heater block, you may break the nozzle at it’s thinnest part! Note the small hole in the heater block is towards the tip of the nozzle.
Holding the heater block in a 14mm spanner (or an adjustable spanner), screw on the tapered brass nut. Tighten the tapered brass nut against the heater block, with a 10mm spanner. This DOES need to be done up tight; the heater block and tapered brass nut lock together, tight on the thread of the nozzle, to ensure good heat transfer from the heater block into the nozzle. The heater block may unscrew a fraction on the nozzle as you do this, but that’s okay.
The cone of the nozzle should continue the cone of the nut, or as close as possible. There shouldn’t be a shoulder between the two, nor should the nozzle be down inside the nut.
Take the PTFE tube. Make sure the ends of the PTFE tube are cut square. (Filament has been inserted into tube just to show the tube against the background.)
You are going to screw the brass Bowden start and the nozzle onto each end of the tube. This will compress the PTFE tube’s inner hole. To allow the filament to run freely in the tube, you need to open out the ends of the PTFE tube first. Use a 2.5mm (2mm is too small, 3mm is too big) drill bit in a small hand chuck, or a slow electric drill.
Gently, and twisting clockwise all the time – never anti-clockwise, whether going in or coming out – use the drill bit to enlarge the inner hole in the PTFE, to a depth of around 15mm. Try to keep the drill as straight as possible into the tube.
Take several goes at it, going a couple of millimetres deeper each time and drawing the PTFE swarf out by keeping twisting clockwise and pulling. The drill should pull the PTFE swarf out with it. Repeat the process at the other end of the PTFE tube.
IMPORTANT! The PTFE tube MUST BE CLEAR OF ALL PTFE SWARF before screwing the nozzle on! Push a piece of filament (use the 50cm piece you cut for the extruder testing) through the tube, which should push out any remaining PTFE swarf. Blow down the tube, from both ends, as well. It is very important to get any PTFE swarf out of the tube, otherwise this will end up in the nozzle the first time you print, blocking it!
Now you’re going to screw the brass Bowden end and the nozzle onto the PTFE tube. To help guide them onto the tube straight, put a piece of filament into the PTFE tube. This will keep the brass Bowden end (and nozzle) and PTFE tube axially in line; you don’t want them screwed on at an angle. Push the brass Bowden end up to the PTFE tube, and push while turning it clockwise. It will start to cut its own thread into the PTFE tube.
If you have difficulty gripping the brass Bowden end, you can use the nozzle instead. With the heater block on it, it is easier to turn. You will have to remove it afterwards, and put the brass Bowden end back on, but it will be much easier the second time.
If you have trouble getting the brass Bowden end started on tube, you can use a pencil sharpener to make a cone on the end of the tube.
Don’t cut too deeply with the pencil sharpener, which will make the cone too deep and long, or it will compress onto the filament when the brass Bowden end, or nozzle, are screwed on.
Keep turning until the Bowden end will not screw on any further. If you then remove the brass union, you should see that the Bowden tube end has been threaded, to a depth of around 8mm.
Using the same process, put the nozzle on the other end of the PTFE tube.
Push a piece of filament through the tube, to check that it moves smoothly, with little or no friction. Check it goes all the way down into the nozzle. It should move nearly as freely as when the brass Bowden end and nozzle were not fitted. If the filament is sticking, you may be able to release it by unscrewing the brass Bowden end and/or nozzle one turn.
The finished Bowden tube and nozzle.

### The cooling system

It’s very important that the top of the nozzle remains cold; if filament melts too high up, the pressure required to extrude will increase, and the nozzle will block and stop extruding.

# | Component | Qty | Type

| Bowden tube and nozzle | 1 | Assembled
736 | Quick-set cooling block | 1 | Hot end
357 | Heatsink | 1 | Hot end
741 | Quick-set hot end fan spacer | 1 | Hot end
| Fan | 1 | Hot end
520 | M3x35mm cap head screw | 2 | Hot end
Fan is 12V (#953) for Ormerod/Mendel, 19V (#846) for Huxley

Take the fan, and push the two M3x35mm cap head screws through the holes in the fan furthest from the fan wire.
Remove any protective film from the acrylic fan spacer.
Place the fan on the fan spacer. Orient the fan spacer as shown. The sticking out part of the fan spacer is used to mount the proximity probe, which sets the nozzle height from the bed, and can automatically compensate for the bed level.
The heatsink goes on next, behind the fan spacer. It only has two holes in it; make sure the M3x35mm cap head screws go through. The fins of the heatsink should face the fan; the solid part is to the back.
Next is the aluminium cooling block. The orientation of this is critical. The heatsink mounting holes are off-centre; orient the block so the holes are closest to the bottom. The long side of the aluminium cooling block will be in contact with the heatsink.
The cooling block mounting holes are only threaded on one side of the block; the cooling block also clamps the hot end in place. The threaded part should be AWAY from the heatsink. The M3x35mm cap head screws will push through the first half of the cooling block, before engaging the thread.
Push the two M3x35mm cap head screws through the four parts, and lightly screw it into the aluminium cooling block. Don’t tighten this up yet; it needs to clamp the nozzle in place. The bottom edge of the heatsink should line up with the bottom edge of the aluminium cooling block, and the solid part of the heatsink should be in good contact with the cooling block.
Now mount the Bowden tube and nozzle. Thread the slotted brass Bowden end up through the aluminium cooling block, followed by the Bowden tube, and then thread the nozzle into cooling block.
The hot end should be aligned with the bottom of the cooling block as shown, with the ‘neck’ of the nozzle just below the cooling block. Orient the heater block so it is under the heatsink and fan, rather than sticking out the back. Tighten the M3x35mm cap head screws, to sufficiently clamp the nozzle in place and pull the heatsink onto the aluminium cooling block, but do not over-tighten them – you will break the fan.
The hot end assembly so far.

## Wiring the hot end

### Thermistor wires

Older kits have the thermistor wiring pre-made. We changed the crimp on the current kits to improve the grip on the thermistor wire, but you’ll need to do the following.

# | Component | Qty | Type | New picture to come

433 | Thermistor wiring – 160mm | 2 | Hot end
197 | 2.4mm Black heatshrink | as needed | Hot end

If your thermistor wiring is supplied without heatshrink on both ends, and the female end looks like this, do the following.
Fold in the two barbs that stick out the side, as shown in the first picture; a small screwdriver or tool with a point is easiest. They need to fold into the crimp, as they will hold the thermistor wire.
Also flatten the top two tabs, so the crimp is smooth. If you put the heatshrink on with them sticking up, they can cut through the heatshrink, and cause a short circuit if they touch other metal.
Put the heatshrink on the end of the wire, covering the crimp but leaving the end open.
Check that it holds the thermistor firmly. You will cover the thermistor with high temperature PTFE heatshrink in the next step; you want as little metal showing as possible between the PTFE heatshrink and the black heatshrink, to avoid short circuits to metal parts of the printer.

### Heater block wiring

### Wiring the hot end connector

#### Wiring diagram

#### Wire colours, related to hot end wiring loom

## Final assembly and mounting

## The tongue

# Hot End Assembly

# Electronics

# Wiring

# Commissioning

# Calibration

# Printing

# Maintenance

# Troubleshooting

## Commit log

2018-08-26 Renaming directory freeCAD to FreeCAD (Learning exercise!)
    [extruder-drive-cover.fcstd]
2018-08-26 Adding FreeCAD files reverse engineered from DXF and STL files.
    [01_547_y-idler-bracket.FCStd, 02_548_y-motor-bracket.FCStd, 03_469_z-motor-brace.FCStd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]
2018-09-04 Build manual copied up to z axis assembly.
2018-09-05 Added pdf version of the manual and have now copied up to the end of the heated bed assembly.
2018-09-05 Build manual to end of extruder section.
2018-09-06 Removed sold works files and continued work on user manual.
    [1044.SLDPRT, 1079.SLDPRT, 1123.SLDPRT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]
2018-09-08 Added x-idler.
    [10_462_x-idler-bracket.FCStd]
2018-10-26 Added a few more files including an assembly model. Subsequently revisited tolerances for transitional fit interference - particularly z-upper, z-lower, and x-idler.
    [04_437_z-lower-mount.FCStd, 05_438_z-upper-mount.FCStd, 10_462_x-idler-bracket.FCStd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]
2018-10-26 Initial assembly and resizing.
2018-10-26 Added some DXF files from other RepRapPro releases & cleaned up the repository.
    [Extrusion_Profile.dxf, bed.DXF, y-cross-rib.DXF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]
